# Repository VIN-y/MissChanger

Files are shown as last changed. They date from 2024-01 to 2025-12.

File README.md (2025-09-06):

# MissChanger

A Stealth Burner tool-change system for Voron 2.4 and Trident.



## Description

MissChanger aims to be a tool-changing upgrade that is compatible with both Voron Trident and Voron 2.4 (Trident compatibility is pending). While also retaining the accuracy and reliability of the MGN9H tapping system of Voron-Tap.

Other features of MissChanger includes:

* The ability to quickly and toollessly convert between tool changer mode and single nozzle mode (for when you need the full print volume of the stock printer).

* Nozzle brush dock. For cleaning the ooze and build-up after tool-change.

## Compatibility

#### Printers:

- Voron 2.4 350 (up to 5 SBs)
- Voron 2.4 300 (up to 4 SBs)

For those who want to adapt MissChanger to your own system. The Bar-Ends are 28mm each, and each dock is 80mm in width. All will be riding in the groove of the 2020 aluminium extrusion frame.

#### Toolhead:

- Stealth Burner

#### Hotend:

Any hot-ends that does not require a custom/extended main-body for the Stealth Burner should works just fine. Nevertheless, the follows are those that has been tested on the reference machine:

- Revo-Voron - Recommended.
  - It is officially supported for the Stealth Burner.
  - It has the the right amount of thermal mass to keep the nozzle temperature stable, while still have decent heat-up and cool-down time.
- Phaetus Dragon - Not recommended.
  - The heater block causing slow heat-up and cool-down. This is not ideal, since it is beneficial to lower the tool temperature when it is docked for a long period of time.
  - The cold side of the hot-end is inadequate to cool PLA in a 30°C+ chamber, eventually causing heat creep if the heater is constantly on.
  - Close proximity between the heater block to the plastic causing deformation. This does not resulted in critical failures, but the affected parts will not work on any other assembly.

#### Extruder:

All extruder that is compatible with the Stealth Burner should works just fine. Nevertheless, any added dimensions on top of the Clockwork 2 might resulted in less print area or space for other tool-heads.

**For v1:** 

* ClockWork 2 (CW2) - Default
  
  * All quoted clearance dimensions are in reference to this extruder.

* Galileo 2 Extruder (G2E)
  
  * The thumbscrew stick out ~8mm to the left. Thus, taking up more docking space than default.

## Assembly

BOM, STLs, and instructions are in the [STL_&_Assembly](./STL_&_Assembly) folder (for the latest and relevant versions), or [MissChanger Archive](https://drive.proton.me/urls/3CDH12JTMW#YhJ5K3t4AadW) (for past versions).

**<u>Note:</u>**

Through testing with material combinations such as ABS-PLA. The window for success for combination of materials that need an enclosure and those that don't are extremely tight. Achieving it require additional hardware (for active chamber temperature control), compromises (such as: weaker layer adhesion, weaker bed adhesion, etc.), and trials-&-errors for every print job. Therefore, it is advised to decide on whether the machine should or should not be enclosed before hand and stick with material combinations that has the same chamber requirements.

## Software

For the latest **Alpha** / **Beta** / **Release** version, instructions are available here: [Klipper_Config](https://github.com/VIN-y/MissChanger/tree/main/Klipper_Config).

The plugin for MissChanger is a fork of [klipper-toolchanger](https://github.com/viesturz/klipper-toolchanger), for [Tapchanger](https://github.com/viesturz/tapchanger), and it is available via GitHub at [VIN-y/klipper-toolchanger](https://github.com/VIN-y/klipper-toolchanger). MissChanger deviate greatly from the design of Tapchanger and Draftshift (Stealthchanger); thus, it's config files are not compatible upstream.

### Recommended software:

- [KIAUH](https://github.com/dw-0/kiauh) - For the purpose of managing Klipper updates, to handle any potential incompatibility issues, whenever there is a major Klipper update.
- [Klipper-Backup](https://github.com/Staubgeborener/Klipper-Backup) - Klipper-Backup is a script for manual or automated GitHub backups. It's Lightweight, pragmatic and comfortable.

## Roadmap

### v1

- [x] ~~Lock in the Tap&Change and dock design for all future versions~~ - v1.1. is the final version for the Tap&Change system for the Stealth Burner
- [x] ~~Print capability test, material combination~~ - Tested with the three most common materials
- [x] ~~Compatibility with smaller Vorons~~ - Have been shown to be compatible with the Voron 2.4 300, via a different assembly configuration (shown in the manual), which should also be compatible with the 250 Vorons.
- [x] ~~USB tool-head support~~ - Nitehawk SB USB tool-head board.
- [ ] Trident compatibility - Full compatibility will be done along side v2.

### v2

- [ ] Trident compatibility - v2 will be built directly on a Trident
- [ ] Support for additional tool-heads - A4T

## Other information

### Status definition

| Terms | Description |
| --- | --- |
| Release | Finalised.<br>All relevant components and documentations are finished and tested. |
| Beta | All relevant components are locked into a release package.<br/>However, without substantial testing or feedback. |
| Alpha | CAD designs locked in.<br>No (or incomplete) documentations. |
| Bleeding  | Everything are subjected to changes. |
| Abandoned | Old design that is no longer being persuaded. |

Note: 

* The .step and CAD project files for all but the most recent version will not be included in this repository, due to the storage/transfer limits of GitHub.

* With user feedback and further testing, the relevant version might be updated to the next tier. However, if significant changes are required, another version will be made and start at the bleeding state; and the current version will no longer be persuaded (i.e. abandoned).

## Recommendations

1. Keep tool-heads as similar as possible. 
   
   1. The more variations there are between tool-heads (i.e. control board, hot-end system, etc.), the more tuning will be need for each of them.
   
   2. Meaningful variants includes: extruder, nozzle size, nozzle material.

2. The following mods are not needed but is **recommended** to enhance the capability of MissChanger:
   
   1. [Calilantern Calibration Tool](https://vector3d.shop/products/calilantern-calibration) - MissChanger requires relatively high dimensional-accurate printed parts, to mate with each others. Therefore, it is recommended that you take the extra steps to calibrate your printer before starting the build.
   2. [Nevermore StealthMax](https://github.com/nevermore3d/StealthMax) - to regulate the chamber temperature, to allow PETG / PLA printing with the door closed; allowing them to be combined with ABS.
   3. [Spool Holder](https://www.printables.com/model/872144-spool-holder-for-2020-aluminium-extrusion) - to hold the spools on top of the machine. There are many ways to get this done, and it depends on the people's specific use-cases. The design linked here is just of my (the developer) own creation.
   4. [Inverted z-chain](https://www.printables.com/model/445298-inverted-z-chain-for-voron) - This is for the Voron 2.4 300mm, or smaller. To clear the space in front of the back gantry extrusion for the umbilicals.

3. The following mods are either **not recommended** or known to be not compatible with MissChanger:
   
   1. GE5C bearing z mount - This mod offer too much flexibility to the gantry, allowing it to sag when the z motors are disabled/un-powered. Nevertheless, it's inclusion will not cause catastrophic problems. You will just need to be careful. (I personally could not be bothered enough to remove mine) 
   
   2. Beefy front idlers - The cut off on the dock can only fit the stock front idlers.
   
   3. AWD - The cut off on the dock can only fit the stock front idlers.

## Sample







## Mods

Community members are encouraged to modify the the CAD where they see fit. They can contribute back to the project by either:

1. Creating a Pull Request, and add the modded files into the [UserMods](./UserMods) folder.

2. Reach out and send me the STEP files.

Modded items are not tested or officially supported. However, if it contains good ideas, it will be implemented into the official design down the line. The originator of the ideas will be included in the list bellow as a contributor.

... So, don't give yourself a weird name, please.

## Support

If you have any question, please FIRST check the [MissChanger Wiki](https://github.com/VIN-y/MissChanger/wiki)

If you still have any question, you can reach me at:

* `@vin` in the [Voron Toolchangers](https://discord.gg/qrb6HXNYxs) discord
* `@vinny_69 V2.6365` in the [VORONDesign](https://discord.gg/voron) discord
* [@vin-y.bsky.social](https://bsky.app/profile/vin-y.bsky.social) on Bluesky

## Contributors

* `@psychosis5150` in the [Voron Toolchangers](https://discord.gg/qrb6HXNYxs) discord
* `@pendorbound` in the [Voron Toolchangers](https://discord.gg/qrb6HXNYxs) discord

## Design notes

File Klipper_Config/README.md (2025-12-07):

# Table of Contents

1. [Introduction](#1-introduction) 

2. [Versions](#2-versions) 

3. [Software](#2-software) 
   
   3.1. [Installation](#31-installation) 
   
   3.2. [Configuration](#32-configuration) 

4. [Calibration](#4-calibration) 
   
   4.0. [Tap&Change burn-in](#40-tapchange-burn-in) 
   
   4.1. [Park position calibration](#41-park-position-calibration) 
   
   4.2. [Input Shaper (optional)](#42-input-shaper-optional) 
   
   4.3. [Calibrate offsets](#43-calibrate-offsets) 

5. [Test and Troubleshoot](#5-test-and-troubleshoot) 
   
   5.1. [Offsets](#51-offsets) 

6. [Tool-change Tuning](#6-tool-change-tuning) 

7. [Slicer Profile](#7-slicer-profile) 

---

# 1. Introduction

Although setting up the config for MissChanger will change some aspects of your printer, it is still recommended that you start the project with a functional printer with Voron-Tap, then add MissChanger and one tool-head at a time.

This document will not guide you through the set up of CAN bus or the physical mounting of the related hardware (i.e. U2C and tool-head board), please refer to the manufacture’s manual for that.

---

# 2. Versions

There are 3 versions for the software, the sample user configs for which are placed in the relevant folder: [1_Main](./1_Main) / [2_Beta](./2_Beta) / [3_Alpha](./3_Alpha).

**Note:** User configs are files that will needed to be set-up on the user's side.

---

# 3. Software

This section aims to provide a guide through the installation process of the software and setup the config.

## 3.1. Installation

To install the [klipper-toolchanger](https://github.com/VIN-y/klipper-toolchanger) plugin, run the following installation script using the following command over SSH. This script will download this GitHub repository to your RaspberryPi home directory, and symlink the files in the Klipper extra folder.

Before installation. For those who are switching branches. You will need to run the uninstall script in below, in **section 3.1.2**.

---

### 3.1.1. Install

1. For normal use:

```
wget -O - https://raw.githubusercontent.com/VIN-y/klipper-toolchanger/main/scripts/install.sh | bash
```

2. For Beta test:

```
wget -O - https://raw.githubusercontent.com/VIN-y/klipper-toolchanger/beta/scripts/install.sh | bash
```

3. For Alpha test:

```
wget -O - https://raw.githubusercontent.com/VIN-y/klipper-toolchanger/alpha/scripts/install.sh | bash
```

*Note 1: You will need to reboot the printer whenever there is an update for the add-on.*

---

### 3.1.2. Uninstall

Some manual changes will still need to be done in the user space (i.e. the section that is accessible via the web interface). These settings / files / folders tend to contain information and calibration values specific to your printer. Thus, it is advised that you create a backup before deletion. This includes:

* The `config` folder

* The `misschanger_settings.cfg` file

* Relevant tool-head config file

* Relevant settings in `printer.cfg`

* `moonraker.conf` registry

To fully uninstall the back-end, run one of the following commands over SSH. Make sure to select the link that is relevant to the version that is currently installed on the printer.

1. For normal use:

```
wget -O - https://raw.githubusercontent.com/VIN-y/klipper-toolchanger/main/scripts/uninstall.sh | bash
```

2. For Beta test:

```
wget -O - https://raw.githubusercontent.com/VIN-y/klipper-toolchanger/beta/scripts/uninstall.sh | bash
```

3. For Alpha test:

```
wget -O - https://raw.githubusercontent.com/VIN-y/klipper-toolchanger/alpha/scripts/uninstall.sh | bash
```

---

## 3.2. Configuration

The **sample configuration files** can be found in the relevant folder above.

The following, starting from **Step 1**, are the recommended steps to get the software up-and-running using the default set of macros. Following the guide will make it easier for you to get support.

The default macros will be managed and updated together with the software stack.

---

### Step -1: Customisation

If you are comfortable with it, you are welcome to by-pass the default macros and play with the configs files to your liking. If you find any errors or room for improvement, feel free to reach out to me to get it fixed, via a GitHub pull request or otherwise.

For building your custom macro:

1. Check where the relevant macro is saved, using the [code stack breakdown](./code_stack_breakdown.pdf) 

2. Download the relevant macro config file, in the [klipper-toolchanger](https://github.com/VIN-y/klipper-toolchanger/tree/main/macros) repository (or straight from your web interface)

3. Import the config file back using the web interface

4. `include` it back into`printer.cfg`

5. Comment-out (or delete) the reference to the file that the new config replaces, in `printer.cfg`

6. Save and Restart

7. Start editing the file to your liking

---

### Step 0: Pre-configuration

These are settings that are in the default Klipper that should to be enabled:

1. [exclude_object] - [Exclude Object](https://youtu.be/QTwRZ_M159Q?si=oV987KDLM-wXsYoE), video guide by [ModBot](https://www.youtube.com/@ModBotArmy) 
2. [skew_correction] - calibrate with [Vector3D CaliLantern](https://vector3d.shop/products/calilantern-calibration) 
3. [input_shaper] - see section **4.2.** 
4. [bed_mesh] - This should have already been configured. However, make sure that there is a bed mesh profile named "default", for the PRINT_START to fallback to if needed.

---

### Step 1: Back-up your running system

Through your web interface:

1. Select all of your config files

2. Download it to your computer

---

### Step 2: Set up printer.cfg

You can check the sample `printer.cfg` in the relevant folder above as reference.
`macro-general.cfg` and `macro-testing.cfg` are optional macros for operations (do not include them in printer.cfg if not used).

Each variable has been given a short description on what they do. Some variables can be used to disable functionalities, such that you will not need to comb through the configs to find and edit them out. The key sections are:

1. Add the **Section Variables** section.
   
   These sections need to be placed just before the **SAVE_CONFIG** section, as shown in the sample `printer.cfg`. Everything below the `Section Variable marker` will be swapped in and out upon the `CONFIG_TOGGLE` macro. If a function setting already exists somewhere else in printer.cfg, the old function will need to be transferred to the new location and updated.
   
   The critical settings that need to be changed are as follows:
   
   - `[gcode_macro _home]` needs to adjusted with the appropriate `xh` and `yh` which represents the centre of the new build area (i.e. 150 (x), 210 (y) for a 300x300 bed).
     
     - `variable_dock` is the indicator of which config is being used.
       
       1. Before installing the dock and other tool-heads, set `variable_dock` to `False`. 
       
       2. Set up T0 (the reference tool-head), see **Step 3**. The `[quad_gantry_level]` (or `z_tilt`, for Trident), and `[bed_mesh]` stay the same the same as stock.
       
       3. After T0 is operational, run `SAVE_CONFIG_MODE`
       
       4. From the web interface, see if the everything below the `Section Variables` has been saved to a .cfg file in the "config" folder.
       
       5. Change `variable_dock` to `True`
       
       6. Install the physical dock. The `[quad_gantry_level]` or `z_tilt` (for Trident), and `[bed_mesh]` **MUST** be updated, as shown in the next 2 bullet points.
   
   - `[quad_gantry_level]`, or `z_tilt` (for Trident), increase the y position of the front 2 `points:` to `130`, to avoid crashing into the dock.
   
   - `[bed_mesh]`, make sure that `mesh_min: 30,130` , to avoid crashing into the dock.

2. If it exists in **printer.cfg**, disable `[safe_z_home]` (comment-out or delete)

3. Add relevant variable (see the code snippet below) under **SAVE_CONFIG**. `[tool_probe T0]` and  `[extruder]` are needed no matter what your setup as it is the reference / default tool-head.
   
   ```
   #*# <---------------------- SAVE_CONFIG ---------------------->
   #*# DO NOT EDIT THIS BLOCK OR BELOW. The contents are auto-generated.
   #*#
   #*# [tool_probe T0]
   #*# z_offset = -0.817500
   #*#
   #*# [extruder]
   #*# control = pid
   #*# pid_kp = 39.282
   #*# pid_ki = 4.365
   #*# pid_kd = 88.386
   #*#
   ```

4. For each additional tool-head, you will need an associated set of  `[tool t(x)]`, `[tool_probe T(x)]`, and `[extruder(x)]` sections. **It is RECOMMENDED** to add and test the tool-heads, one at a time. For example:
   
   ```
   #*# [tool T1]
   #*# gcode_x_offset = -0.225000
   #*# gcode_y_offset = 0.590625
   #*# gcode_z_offset = 0.470000
   #*#
   #*# [tool_probe T1]
   #*# z_offset = -0.622500
   #*#
   #*# [extruder1]
   #*# control = pid
   #*# pid_kp = 33.912
   #*# pid_ki = 3.325
   #*# pid_kd = 86.477
   ```

*NOTE 1: Your printer will be throwing errors at this point, until the software is fully setup.* 

*NOTE 2: The variables will need to be calibrated to match your hardware.*

---

### Step 3: Make the reference tool-head config file

Use the `T0-SB2209-Revo-LDO.cfg` in [Sample_Config](./Sample_Config) folder as reference.

1. Transfer the items relating to the tool-head from your `printer.cfg` to a separate file:
   
   * `[mcu EBBCan0]` - the MCU for your tool-head, named to your liking, i.e. EBBCan0.
   
   * `[adxl345]` - The accelerometer on the tool-head.
   
   * `[resonance_tester]` 
   
   * `[temperature_sensor]`
   
   * `[extruder]`
   
   * `[tmc2209]` - that is associated extruder motor
   
   * `[verify_heater]`
   
   * `[heater_fan]`
   
   * `[neopixel]` - if applicable
   
   * `[tool_probe]` 
     
     <mark>NOTE:</mark> the `activate_gcode:` for the item has been replace with the macro `_TAP_PROBE_ACTIVATE`, with the flag `HEATER=extruder`. This flag <mark>NEEDS TO BE SET TO THE RIGHT "EXTRUDER"</mark>. Failure to do so may result in damage bed surface.

2. Replace `[fan]` with `[fan_generic T0_partfan]`

3. Add the following item and macro:
   
   * `[gcode_macro T0]` - for tool switching
   
   * `[tool T0]` - associate the items above to T0 and provide tool specific variables (which will need to be adjusted later).

---

### Step 4:

Include tool-head config in the session variables are in `printer.cfg`, as shown in the relevant sample config.

*Note: At this point, the printer should be able to have a firmware restart without (or with minor) errors.* 

---

### Step 5: Calibrate and test T0

1. For safety reasons, remove the dock and any attached tool-head other than T0.

2. Run `FIRMWARE_RESTART` and fix any problem that arise ;)

3. Run `G28` and `QUAD_GANTRY_LEVEL` 

4. Check that:
   
   * The printer homes Y before X
   
   * Quad gantry level front points are at Y = 130
   
   * Extruder PID is correctly set and applied (no error / no bouncing temperature)

5. Re-mount the dock

6. Calibrate extruder `rotation_distance`

7. Calibrate heater PID

8. Calibrate the park position, see **section 4.1.** 

9. Calibrate the `z_offset`, see **section 4.3.** 

10. (optional) Calibrate input shaper, see **section 4.2.** 

11. Save & Restart

---

### Step 6: Make the next tool-head and its config file

1. Follow the hardware assembly guide from the manufacture of the relevant hardware, i.e extruder, tool-head board, etc.

2. Mount the dock and temporarily mount the new tool-head to the dock.
   
   <mark>CAUTION:</mark> **DO NOT** try to make the printer pick up the new tool yet.

3. Use `T1-SB2209-Revo-LDO.cfg` (and others) config file as references. Make, calibrate, and test the config files for the other tool-heads.

4. Include tool-head config in the session variables in `printer.cfg`, as shown in the code block in **step 2.3**.

5. Copy and paste the associated set of `[tool t(x)]`, `[tool_probe T(x)]`, and `[extruder(x)]` to the **SAVE_CONFIG** section, if they are not already there.

6. Save & Restart

---

### Step 7: Calibrate and test tool-head

If this is the first tool-head you made beside the reference tool-head, then you will need to test the max y position of your set up:

1. Run `G28`

2. Manually nudge the tool-head to right behind (but not touching) a docked tool (via the web interface), 

3. Note down the Y position of that location

4. If the y location is greater than 120 mm, then you will need to update the `params_safe_y` value in `[toolchanger]` in `misschanger_settings.cfg`

5. Save & Restart

Otherwise:

1. Calibrate extruder `rotation_distance`

2- Calibrate heater PID

3. Save & Restart

4. Run `G28` and `QUAD_GANTRY_LEVEL`

5. Calibrate the park position, see **section 4.1.** 

6. Calibrate the `z_offset`, see **section 4.3.** 

7. (optional) Calibrate input shaper, see **section 4.2.** 

---

### Step 8: Other macros

* `macro-general.cfg`

* `macro-test.cfg`

These configs tend to be points of customisation for many. Therefore, the included files are intended to be inspirations for your own macros. They contain commands and functionalities that may not be needed or are not relevant to your printer.

---

### Step 9: Single tool-head config

1. Run `SAVE_CONFIG_MODE` to save the current setup.

2. Check if the save was made correctly, in the **config** folder.

3. In the Section Variable section in **printer.cfg**:
   
   1. Comment out all included tool-head configs other than T0
   
   2. Under `[gcode_macro _home]`:
      
      1. Set an appropriate `xh` and `yh` which represent the centre of the new build area (i.e. 150 (x), 210 (y) for a 300x300 build plate).
      
      2. Set `variable_dock` to `False`
   
   3. Revert `[bed_mesh]` and `[quad_gantry_level]` to the original values of the stock machine (without the tool-changer bits)
   
   4. Delete all `#*# [tool T(x)]`, `#*# [tool_probe T(x)]`, and `#*# [extruder(x)]` objects, under the `SAVE_CONFIG` section.
      
      * **EXCEPT:** the `#*# [tool_probe T0]` and `#*# [extruder]` object.  

4. Save, but no restart is needed.

5. Run `SAVE_CONFIG_MODE` and check if the file is correctly saved.

Now, the `CONFIG_TOGGLE` macro will allow you to toggle between these 2 configs.

---

# 4. Calibration

This section assumes that the new tool-head has been assembled, wired up, and has been recognised by Klipper.

## 4.0. Tap&Change burn-in

The following steps are for the burn-in of the Tap&Change mechanism. This is so that it can sort out any misalignment due to print tolerance and assembly. Through testing, it has been shown that this only need to be done once for every Tap&Change rail-side (there is only one in the system).

1. Setup to the variable for `SHAPER_CALIBRATE`, to your liking

2. Manually mount T0

3. Run `G28`

4. Bring the tool-head to 10 mm above the centre of the bed

5. Turn on the bed heater

6. Turn on the chamber fan (if exist)

7. Wait until the tool-head (i.e. "Extruder") temperature reached ~40°C (or ~10 mins if you don't have a chamber temperature sensor)

8. Run `SHAPER_CALIBRATE` - Note: This is only meant to shake the tool-head around in its mount. Do not save the input shaper result.

9. Repeat step 4 - 8 until the tool-head can fall into the mount on it's own weight when manually removed and replaced.

---

## 4.1. Park position calibration

1. Run `G28` and `QUAD_GANTRY_LEVEL`  - if not already done

2. Run `G1 Z150 F9000` 

3. Run `STOP_TOOL_PROBE_CRASH_DETECTION` 

4. Loosen the bolts on the bottom of the dock of the relevant dock (so it will spin around the bar)

5. On the web interface, in `Setting > Control` add `0.1` and remove `100` in the `Move distance increments X & Y axes (in mm)` 
   
   *Note: This is temporary for this step only, and can be reverted later.*

6. Set the dock toolhead cradle at the 'empty' position in the dock assembly, i.e. at the bottom of the ramp.
   

7. Use the web interface, nudge the tool-head into the correct x-position. This can be tested by nudging the y-position in and out to see which side of the tool-head touches the dock first. Then adjust the x-position such that both sides of the dock touch the tool-head at the same time.
   

8. Copy and paste the current x-coordinate into the `params_park_x:` of the config file of the current tool-head

9. Save it, **BUT DON'T RESTART**

10. Nudge the y-position until the toolhead is fully seated in the dock toolhead cradle.
    
    1. Make sure that the whole dock-bar isn't being lifted up in the extrusion grooves.
    
    2. Make sure the toolhead is fully seated in the dock toolhead cradle before it starts being lifted up the ramp. Check it by nudging it back and forth 10mm.
    
    3. If step 10.1 and 10.2 are not met, adjust the Bar End spacers to fit. TIP: the distance for the spacers should be the same for both sides.

11. Tighten the bolts on the bottom of the dock (locking it in place)

12. Nudge the y-position until the dock is at the peak of the ramp. The dock is tough enough to handle a bit of pressure from the gantry so you can keep nudging the y-position until the dock flexes a bit, then back it off.

13. Run:
    
    ```
    G91
    G1 Y+80 F6000
    G90
    ```

14. Copy and paste the current y-coordinate into the `params_park_y:` of the config file of the current tool-head

15. Save it

16. Run `FIRMWARE_RESTART`

17. Run the `TEST_DOCKING` macro

---

## 4.2. Input Shaper (optional)

*Note: To avoid Klipper from throwing errors, the parameters for input shaper are pre-populated in* `toolchanger.cfg` *and in each tool-head config file. Nevertheless, it is best to calibrate it for each available tool-head.*

1. Enable (un-comment) the `[adxl345]` and `[resonance_tester]` in the config of the tool-head that is to be calibrated

2. Disable (comment out) the `[adxl345]` and `[resonance_tester]` in the config of the other tool-heads

3. Save & Restart

4. Mount the tool-head that is to be calibrated

5. Run `G28` and `QUAD_GANTRY_LEVEL`

6. Run `SHAPER_CALIBRATE` - **BUT, DO NOT SAVE**

7. From the console output, save the following parameters into the tool-head config (at the bottom of the `[tool Tx]` section)
   
   ```
   params_input_shaper_type_x: ...
   params_input_shaper_freq_x: ...
   params_input_shaper_damping_ratio_x: ...
   params_input_shaper_type_y: ...
   params_input_shaper_freq_y: ...
   params_input_shaper_damping_ratio_y: ...
   ```

8. Save & Restart

---

## 4.3. Calibrate offsets

### 4.3.1. Calibrate reference z-offset

1. Mount tool-head T0

2. Go to T0 config file. Make sure:
   
   - `z_offset` under `[tool_probe T0]` is commented out
   
   - Every other offsets to `0`; i.e. `x_offset` and `y_offset`
   
   - Save it, **BUT DON'T RESTART**
   
   

3. Run `G28` and `QUAD_GANTRY_LEVEL` 

4. Run `PROBE_CALIBRATE` on the console and go through the process with the normal paper test.

5. <u></u>Run `SAVE_CONFIG` - which will restart your printer

6. Go to `printer.cfg`

7. Copy the z-offset value from:
   
   ```
   #*# [tool_probe_endstop]
   #*# z_offset = {value}
   ```
   
   And, paste it to:
   
   ```
   #*# [tool_probe T0]
   #*# z_offset = {value}
   ```

8. Delete:
   
   ```
   #*# [tool_probe_endstop]
   #*# z_offset = {value}
   ```
   
   *Note: It will not be used regardless of whether it is there or not.*

9. Save & Restart

*Note: It is key that you get the z_offset correct for the T0, as it will be used to extrapolate other offsets later on. Therefore, it is worth diverging from these instruction if you have a preferred way to set your the z-offset.*

---

### 4.3.2. Calibration probe setup

At this stage, you should have:

- The calibration probe assembled, tested, and installed

- T0 z-offset calibrated

This section will guide you through the calibration of the machine specific variable `trigger_to_bottom_z`, which will allow you to automate the z-offset of the tool-heads that are not T0. *Note: This should be your go to variable to adjust whenever you ran into z-offset issue.*



### Setup:

1. Open `misschanger_settings.cfg`

2. Setup `[tools_calibrate]` with the correct `pin`, for the LubeBalls (or Nudge)

3. Save and restart

4. Test calibration probe, by touching the it with your finger and run `TOOL_CALIBRATE_QUERY_PROBE`
   
   

5. Open `printer.cfg`

6. Set the approximate X and Y location of the Nudge pin in `[gcode_macro _static_variable]`. Note: you can find out the XY position by homing and moving the tool-head in place with the web UI or Klipper Screen.
   
   

7. Save and restart

### Steps:

1. Go to `printer.cfg` and record the `z-offset` for `[tool_probe T0]`, which should be at (or near) the bottom of the file

2. Mount tool-head **T0** and make sure it's nozzle is clean

3. <mark>**!!! MAKE SURE THE CALIBRATION PROBE IS NOT MOUNTED !!!**</mark>

4. Run `G28` and `QUAD_GANTRY_LEVEL`

5. Mount the calibration probe to the bed.

6. Run `CALIBRATE_TRIGGER_BOTTOM`. If it is a fresh calibration probe, it is worth redoing this step until the suggested value is consistent at +/- 0.005mm. 

7. Copy the proposed offset on the console to the `trigger_to_bottom_z:` in `[tools_calibrate]`.

8. Save and restart

9. Run `CALIBRATE_OFFSETS TOOL=0` - But, **DON'T RESTART**

10. Check if proposed z-offset to be +-0.01mm of the recorded `z_offset` in **step 1**.

11. Run `CALIBRATE_OFFSETS TOOL=0` 2-3 more times to make sure the measured value is consistent.

**Your calibration probe is ready.**

*Note: It is worth mentioning that there are other ways to calibrate your offsets, such as the visual based solution from [Ember](https://www.emberprototypes.com/products/cxc) or the calibration print that you can get from [Printables](https://www.printables.com/model/201707-x-y-and-z-calibration-tool-for-idex-dual-extruder-). Each have their pros and cons in terms of accuracy and cost. However,  a physical contact probe is currently the only way to automatically calibrate all relevant offsets.*

---

### 4.3.3. Other tool-head(s)

### Steps:

1. <mark>**!!! MAKE SURE THE CALIBRATION PROBE IS NOT MOUNTED !!!**</mark>

2. Make sure all tool-heads are cold (near room temperature)

3. Make sure all nozzles are clean

4. Make sure all tool-head config file (except T0) has the following variables disabled (commented out):
   
   - `gcode_x_offset` 
   
   - `gcode_y_offset` 
   
   - `gcode_z_offset` 
   
   - `z_offset` 
   
   

5. Save it, **BUT DON'T RESTART**

6. Mount tool-head T0

7. Run `G28` and `QUAD_GANTRY_LEVEL`

8. Mount the calibration probe

9. Run `CALIBRATE_OFFSETS` - the process is automatic, but you can specify a specific tool-head

10. Run `SAVE_CONFIG`

If you has the calibration probe. There is a likelihood that the `CALIBRATE_OFFSETS` procedure cannot be completed. If so:

1. set `variable_calibration_abs_z_seperately` to `1` in `[gcode_macro _static_variable]` in **printer.cfg**.

2. Mount tool-head T0

3. Run `G28` and `QUAD_GANTRY_LEVEL` 

4. Run `CALIBRATE_ABSOLUTE_Z` 

5. Run `SAVE_CONFIG`

---

### 4.3.4. Clean dock

#### Steps:

1. Install the clean dock in your preferred slot on the gantry

2. Approximate the x position of the centre of the dock (where the brush is)

3. Add the aforementioned x position into `printer.cfg`. In `variable_clean_dock_x` under `[gcode_macro _static_variable]`.

#### Optional steps, for auto mid-print clean:

1. Set-up the `variable_clean_threshold` under `[gcode_macro _static_variable]`. "150" means that the print needs to take up ~50% of the bed before triggering a mid-clean print.

2. List the materials that need to have their associated tool-head cleaned in `misschanger_settings.cfg`. For example:
   
   ```
   params_need_clean_materials: ['PETG', 'FLEX']
   ```

---

# 5. Test and Troubleshoot

## 5.1. Offsets

It is important to test if the `z_offset` and `gcode_z_offset` are set-up and applied correctly. A misconfigured `z_offset`/`gcode_z_offset` can cause the nozzle to be dragged on the bed, risking damage. Please follow the steps below to test the config, before you start printing.

### Part 1: Check the z_offset of T0

1. Make sure the printer is cold (near ambient temperature).

2. Run `G28` and `QUAD_GANTRY_LEVEL` with T0

3. Run `G1 X175 Y235 Z10 F9000` (centre of print area)

4. Run `G1 Z0 F9000` 

5. Test the z-offset with the paper test. - If it is good then you set up the `trigger_to_bottom_z` value correctly.

6. If it does not work:
   
   1. baby step the z position to the correct position
   
   2. adjust `trigger_to_bottom_z` accordingly using the baby stepped amount.
   
   3. then, rerun `CALIBRATE_OFFSETS TOOL=0`.
   
   4. retry step 1 to 3 until the paper test succeeds.

### Part 2: Check the gcode_z_offset of the other tools

1. Go through step 1 and 2 of **Part 1**, above.

2. Switch to next tool, via the web UI or Klipper Screen.

3. Go through step 3 to 6 of **Part 1**, above.

4. If it does not work. rerun `CALIBRATE_OFFSETS TOOL=[x]` for that tool-head (or all of them).

### Part 3: gcode_x_offset and gcode_y_offset

To validate `gcode_x_offset` and `gcode_y_offset`, you just need to print something and see if they are set-up and applied correctly. Alternatively, you can also buy and use [Ember Camera Assisted XY](https://www.emberprototypes.com/products/cxc) to validate them.

---

# 6. Tool-change Tuning

The speed and path of the default tool-change routine in `misschanger_settings.cfg` is tuned for reliability. It is slower and has more steps than needed.

For a smooth running MissChanger. The `params_path_speed` can be increased and some of the "Wiggle wiggle", in the path, can be disable.

---

# 7. Slicer Profile

## 7.1. Custom Start G-code

Copy and paste the following code into your slicer.

*Note: It needs to stay as a single line of gcode.*

```
PRINT_START BED_TEMP=[first_layer_bed_temperature] FIRST_LAYER_PRINT_SIZE=[first_layer_print_size] TOOL=[initial_tool] TOOL_TEMP={first_layer_temperature[initial_tool]} {if is_extruder_used[0]}T0_TEMP={first_layer_temperature[0]} T0_Fil={filament_type[0]}{endif} {if is_extruder_used[1]}T1_TEMP={first_layer_temperature[1]} T1_Fil={filament_type[1]}{endif} {if is_extruder_used[2]}T2_TEMP={first_layer_temperature[2]} T2_Fil={filament_type[2]}{endif} {if is_extruder_used[3]}T3_TEMP={first_layer_temperature[3]} T3_Fil={filament_type[3]}{endif} {if is_extruder_used[4]}T4_TEMP={first_layer_temperature[4]} T3_Fil={filament_type[4]}{endif} {if is_extruder_used[5]}T5_TEMP={first_layer_temperature[5]} T5_Fil={filament_type[5]}{endif}
```



Also. Disable the following option:



## 7.2. Slicer Bed Shape

The printer bed shape need to be set as shown below to avoid collisions with the dock during printing.

Depending on the umbilical mounting solution on the tool-head side, the lost y can be between 120mm to 140mm.

*Note: It can be seen here that the max print height was set to 235mm. This is recommended for new machines to avoid umbilical tangling. However, if you are willing to do some tuning to the tension of the umbilical or add a top hat to the system, the max print height can be increased to 250mm or 300mm.*

### For printers with 350mm beds:



### For printers with 300mm beds:



## 7.3. Multiple Extruders

Enable **Ooze Prevention**.

This setting will allow you to reduce the docked nozzle temperature, to prevent over cooking the filament. Furthermore, it will effectively act as reheat command for when the system is recovering from a failed tool-change.

Even if you don't want it to drop the temperature, still enable it, then set the `Temperature variation` to -25°C. This setting will emit a nozzle heating command after tool-change.



## 7.4. Speed profile

Although, you might want to tune your own speed profile for the best performance. Here is a slow and reliable profile to get you started with.



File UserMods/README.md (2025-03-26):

## For all mods to the CAD

Please put your custom files here, in a folder of your Github profile name (or Discord name), i.e.:

`[your-profile-name]`/`[custom-files/folder]`

Please also includes a `README.md` file, with the descriptions / instruction of for the mod. Additional photos will also be appreciated.

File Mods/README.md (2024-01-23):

## For all mods to the software / CAD
Please put your custom files here, in a folder of your Github profile name. i.e.:

`[your-profile-name]/[custom-files/folder]`

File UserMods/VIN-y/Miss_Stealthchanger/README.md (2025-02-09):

# Miss Stealthchanger

This is a mod to the Stealthchanger v1.1 to make it compatible with MissChanger's docking system. See it working via this [YouTube video](https://youtube.com/shorts/WBkSGx4JyOY?si=XXWXMF8TNKqw9jsA).

## Software:

* No software change needed

## Hardware:

* This mechanism replaces the Tap&Change system. It includes:
  
  * SC_TH-side_mod.stl
  
  * Shuttle_Keeper_6mm_MGN12H.stl
  
  * Shuttle MGN12 (Without belt grooves).stl
  
  * X-trigger_v1-Body001.stl

* Stealthchanger Assembly Guide is attached

* This mod ONLY support the Stealth Burner version of Stealthchanger

* For other mounting options of the Shuttle, visit [DraftShift/StealthChanger](https://github.com/DraftShift/StealthChanger)

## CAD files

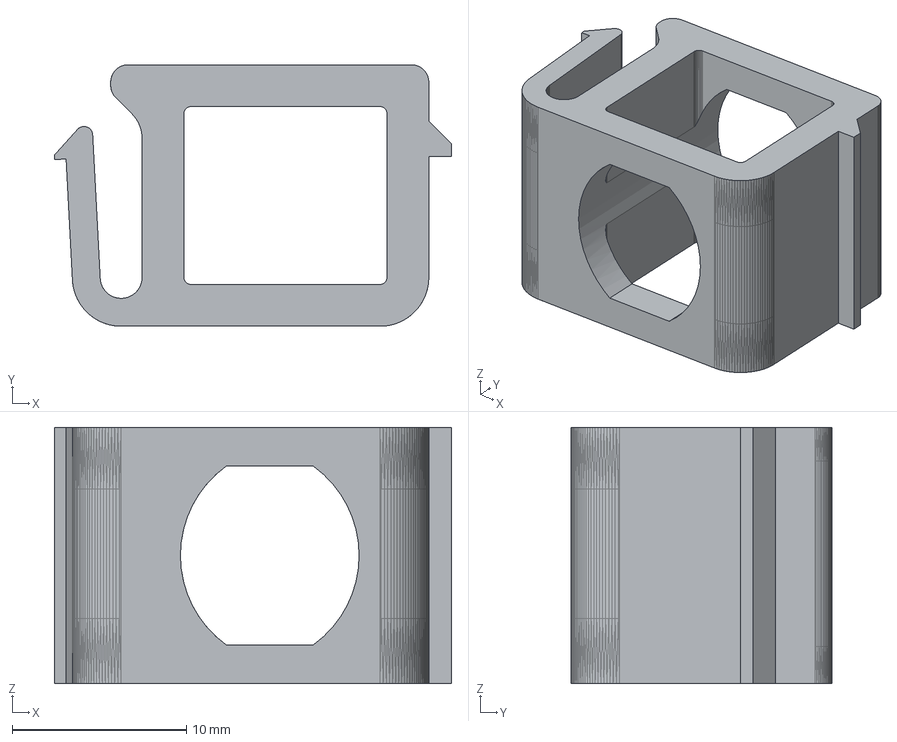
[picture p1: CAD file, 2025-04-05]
CADs/v1_MVP/Optional/DC_Barrel_Panel_Mount/11_DC_Barrel_Keystone-Keystone.step
22.8 x 15.0 x 14.7 mm

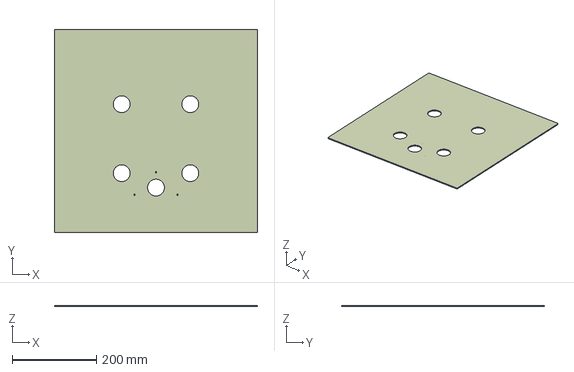
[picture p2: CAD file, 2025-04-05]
CADs/v1_MVP/Optional/Nevermore_Stealthmax/10_NM_StealthMax_Mod-Top_Panel_350_Drill.step
483.0 x 483.0 x 3.00 mm

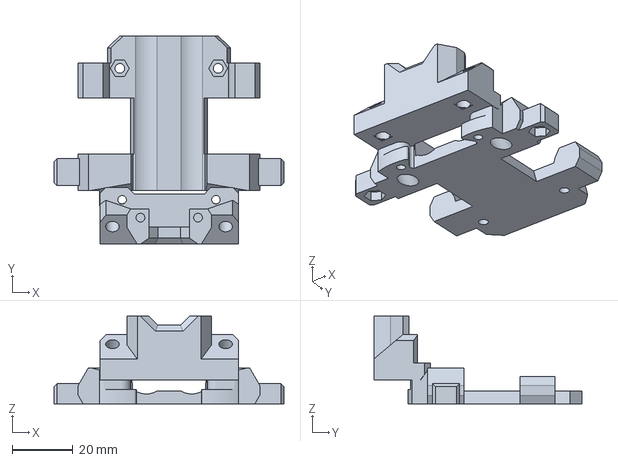
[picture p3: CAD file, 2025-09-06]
STL_&_Assembly/1_Tap&Change/Tap&Change-Front_TH_Side_Mono.3mf
76.0 x 68.9 x 29.0 mm

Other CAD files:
STL_&_Assembly/6_Optionals/Nevermore_StealthMax/M_2.0_MainChamber.stl
STL_&_Assembly/1_Tap&Change/Endstops_Assembly-v0.6.stl
CADs/v1_MVP/Endstops_Assembly-v0.6.step
STL_&_Assembly/1_Tap&Change/MGN9_Assembly_Tool.stl
CADs/v1_MVP/Tap&Change-v3.1_TH_Side.step
STL_&_Assembly/2_XLR_Panels/z_chain_bottom_anchor_mirror.stl
STL_&_Assembly/3_Dock/Bar_Ends Holder_A v1_9.stl
STL_&_Assembly/4_Calibration_Probe/Calibration_Probe_Dock_x2.stl
STL_&_Assembly/4_Calibration_Probe/Lubeballs/Luballs_Probe-Top.stl
STL_&_Assembly/4_Calibration_Probe/Nudge/wobbler_5mm.stl
STL_&_Assembly/5_Others/CW2-umbilical_anchor/CAN_Cable-Holder.stl
STL_&_Assembly/5_Others/G2E-umbilical_anchor/G2E_standoff_2_mod.stl
STL_&_Assembly/5_Others/PTFE_Panel.stl
STL_&_Assembly/6_Optionals/DC_Barrel_Panel_Mount/11_DC_Barrel_Keystone-Keystone.stl
UserMods/Psychosis5150/Idle Dock Mount/Dock Mount.stl
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

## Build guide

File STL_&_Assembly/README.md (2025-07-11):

# Introduction

This folder contains the STLs, config files, and instructions for both the latest and past version of MissChanger.

Each versions are enclosed in their own folder in the [MissChanger Archive](https://drive.proton.me/urls/3CDH12JTMW#YhJ5K3t4AadW). These folder should contains all the information that is available and relevant to that version of the system. Nevertheless, this directory structure was not fully fleshed out until v1.1, and CAD models reservation were not properly done until v1.2. Therefore, the documentation for versions that are older than v1.1 might not be functional, and no CAD file older than v1.2. is available.

## Situational / Optional / Mods

These following attachments are extras that will expand the capability of tool-changer system. Nevertheless, they were developed by others and does not share the same design language as MissChanger (i.e. difference print parameters).

| Mod | Description |
| --- | --- |
| [Nevermore Stealth Max](./6_Optionals/Nevermore_StealthMax)<br> + [DC Barrel Panel Mount](./6_Optionals/DC_Barrel_Panel_Mount) | - With modded flow chamber<br>- Cable management for Nevermore Stealth Max |
| [Galileo 2 + LDO Nitehawk SB USB cable strain relief](./5_Others/G2E-umbilical_anchor) | For Galileo 2 + LDO Nitehawk SB USB |
| [Inverted z-chain](https://www.printables.com/model/445298-inverted-z-chain-for-voron) | Recommended for the Voron 2.4 300mm, or smaller. To clear the space in front of the back gantry extrusion for the umbilicals. |

# Summary

| Version | Status | Remarks |
|:---:|:---:| --- |
| v0.0 | Abandoned | The design has been proven to lack durability in the testing phase. |
| v1.0 | Beta | Although functional, several reliability and usability problems were found. |
| v1.1 | Alpha | Fixes problems found in v1.0.<br/>Tool-changer reliability tested and proven. It will be carried forward, unless stated otherwise.<br/>The Nevermore StealthMax is added as optional chamber temperature management. |
| v1.2 | Beta | Add support for Voron 2.4 300mm.<br/>Add support for USB tool-heads.<br/>Add G2E official support.<br/>Revamp software stack and bug fixes.<br/>Preliminary Trident support. |
| v1.2.1  | Beta | Klipper compatibility fix.<br/>Move fan control to the the back-end, for smoother operation.<br/>Add more user controllable variables.<br/>Separate the `Klipper_Config`, to allows for software hot fix without the need to create another release. |
| v1.2.2  | Release | Minor updates to CAD.<br/>Update documentations. |

# Change Log

### v1.2.2 - minor update for Release 1

- Update Endstops Assembly for easier post-processing.

- Update documentation.

### v1.2.1 - Hot fix and add features

* Klipper compatibility fix.

* Move fan control to the the back-end, for smoother operation.

* Add more user controllable variables.

* Separate the `Klipper_Config`, to allows for software hot fix without the need to create another release.

### v1.2 - Polish hardware and revamp software

- Remigrating the project back to FreeCAD, because Ondsel ran out of funding and shutdown.

- Added official Nitehawk SB USB tool-head board.

- Voron 2.4 300 compatibility established, tested by `@psychosis5150`.

- Update the design of the Nudge Mount, for broader compatibility and increase durability.

- Update XLR panel design for better compatibility and alignment.

- Add official support for the G2E.

- Introducing the Lubedballs probe, as an alternative to the Nudge probe. Intended as an easier system to build.

- Fix some compatibility issue for Voron Trident.

- Bug fixes and revamp software stack:
  
  - Added changes from [DraftShift/klipper-toolchanger](https://github.com/DraftShift/klipper-toolchanger). This fork faster moving and has more features on top of [viesturz/klipper-toolchanger](https://github.com/viesturz/klipper-toolchanger). Nevertheless, it is noted that Viesturz is still slowly adding features to his extension. Therefore, future updates to [VIN-y/klipper-toolchanger](https://github.com/VIN-y/klipper-toolchanger) (for MissChanger) may adopt features from either of the for mention repository, where they may fit for the project.
  
  - Deprecate `multi-fan` to re-enable the ability to control the part cooling fan with the GUIs.
  
  - Establish the structure of the software stack, to have a low barrier of entry while still allow customisation.
  
  - Revamp the tool-change routine, to avoid firmware crashing or unsafe movement during pick-up.
  
  - Add fail to drop-off detection.
  
  - Fixed the bug where the `gcode_z_offset` not correctly clear out after tool-change.
  
  - Revamped `CALIBRATE_OFFSETS` routine:
    
    - To check for proper probe placement before starting the session.
    
    - Add an option to run the routine with or without absolute z calibration. For over sensitive probes.
  
  - Add a macro to calibrate trigger bottom. So the printer don't need to be restarted and homed multiple times during calibration.
  
  - Fix the bug where the QGL failure is not detected in `PRINT_START`.
  
  - Fix compatibility issue with PrusaSlicer 2.9.0+, where the XY coordinate of the wipe tower is no longer get emitted.
  
  - Fix the bug with part cooling fan speed being stuck at random values midway through the print.
  
  - Add the function to save z_offset baby-steps.

### v1.1 - Fixing problems with v1.0 and further testings

- Migrate the project files to Ondsel, the CAD software, and tighten up part-to-part tolerances

- Adds magnets to the docking system to hold onto the tool-head more securely when docked

- Increase wall thickness of the Tap&Change pieces, making it more durable

- Add door buffer, for clearance of the docked tool-heads.

- Add silicon liner layer for nozzle plug, to avoid PETG-caused damage.

- Passed reliability test with 4100 continuous tool-changes at random z-positions

- Adds support for the Nevermore StealthMax, with a modified flow chamber with output switch.

- User feedback. A design flaw has been discovered in the XLR Panels, which cause slight incompatibility with smaller Voron.

- Testing has shown that the better air flow control can significantly increase the utilisation of the bed heater for chamber heating.

- Multi-material experiments show that the tool-changer will benefit from chamber temperature management. Lower chamber temperature will allow ABS to be combined with PLA / PETG. However, the result is mixed, as many ABS print came out poorly due to the lower chamber temperature.

### v1.0 - First Beta

This is the first version of MissChanger for others to pick-up and build upon. Through testing, it shows the following pros:

- The tool-change mechanism is reliable (with ~5000 cycles on T0, thus far)

- The stock front z-motors can carry the weight of the dock and 4 tool-heads, ~2.5 kg

- The safety mechanism functions as intended, where the dock's Bar Ends will flex, before the dock are pushed into misalignment, before the front z-motors skip steps, before any damage is done. - This is in the event that the front gantry tilts down too far, causing the idlers to crash into the bottom corners of the dock.

- The umbilical does not get tangled until at least Z200, and printer is still functional up to Z250 with some limitation around the edge of the build area.

- The system can be toggled between single tool-head and multi-tool-heads mode without the use of any tool, in about 20-60s.

- Tool-change speed is relatively fast, ~8s

- Probe accuracy is very high, with `samples_tolerance: 0.00275` on all tool-head

- The Nudge calibration probe is very accurate and reliable

Nevertheless, the tests have also reveals the following cons:

- Tap&Change pieces are too fragile and would crack in the event of tool-head crash or with lower tolerance printed parts

- Incompatibility with GE5C bearing z mount for the Voron 2.4

- Incompatibility with front idler mods

- Tolerance for front gantry tilt is still too low

- Friction mounted tool-heads are susceptible to be bumped loose by door closing

- There are limits to the material combination in a tool changer, due to the shared chamber and bed temperatures

- The PTFE tube influences the curve of the umbilical more than everything else, beside the top panel

- Input shaper result is worse than that of the original Voron Tap

- This version was quick to be pushed to beta, because there was only one MissChanger in the work. Future versions will be given more time at each tier, as more people get on board with the project

### v0.0 - Original idea

* This was the original idea for MissChanger, which was developed up to the point where it can be used for test prints. It was discovered that the mechanism would wears down after ~2000 cycles and lost the precision needed for Quad Gantry Level.
  
  No further work will be done for this design, and documentations are not available.

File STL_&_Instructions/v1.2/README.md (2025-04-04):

# Table of content

1. [Introduction](#1-introduction) 

2. [Hardware](#2-hardware) 
   
   2.1. [MissChanger Core Assembly](#21-misschanger-core-assembly)
   
   2.2. [Situational / Optional / Mods](#22-situational--optional--mods) 

3. [Software](#2-software) 
   
   3.1. [Installation](#31-installation) 
   
   3.2. [Configuration](#32-configuration) 

4. [Calibration](#4-calibration) 
   
   4.0. [Tap&Change burn-in](#40-tapchange-burn-in) 
   
   4.1. [Park position calibration](#41-park-position-calibration) 
   
   4.2. [Input Shaper (optional)](#42-input-shaper-optional) 
   
   4.3. [Calibrate offsets](#43-calibrate-offsets) 

5. [Test and Troubleshoot](#5-test-and-troubleshoot) 
   
   5.1. [Offsets](#51-offsets) 

6. [Tool-change Tuning](#6-tool-change-tuning) 

7. [Slicer Profile](#7-slicer-profile) 

---

# 1. Introduction

Although the setting up the config for MissChanger will change some aspects of your printer, it is still recommended that you start the project with a functional printer with Voron-Tap, then add MissChanger and one tool-head at a time.

This document will not guide you through the set up of CAN bus or the physical mounting of the related hardware (i.e. U2C and tool-head board), please refer to the manufacture’s manual for that.

---

# 2. Hardware

## 2.1. MissChanger Core Assembly

The following manual is for the core components that are needed to get MissChanger up and running.

MissChanger Assembly Manual: [MissChanger_Assembly_Manual](./MissChanger_Assembly_Manual.pdf).

## 2.2. Situational / Optional / Mods

These following attachments are extras that will expand the capability of tool-changer system. Nevertheless, they were developed by others and does not share the same design language as MissChanger (i.e. difference print parameters).

| Mod | Description |
| --- | --- |
| [Nevermore Stealth Max](./6_Optionals/Nevermore_StealthMax)<br> + [DC Barrel Panel Mount](./6_Optionals/DC_Barrel_Panel_Mount) | - With modded flow chamber<br>- Cable management for Nevermore Stealth Max |
| [Galileo 2 + LDO Nitehawk SB USB cable strain relief](./5_Others/G2E-umbilical_anchor) | For Galileo 2 + LDO Nitehawk SB USB |
| [Inverted z-chain](https://www.printables.com/model/445298-inverted-z-chain-for-voron) | Recommended for the Voron 2.4 300mm, or smaller. To clear the space in front of the back gantry extrusion for the umbilicals. |

---

# 3. Software

This section aims to provide a guide through the installation process of the software and setup the config.

## 3.1. Installation

To install the [klipper-toolchanger](https://github.com/VIN-y/klipper-toolchanger) plugin, run the following installation script using the following command over SSH. This script will download this GitHub repository to your RaspberryPi home directory, and symlink the files in the Klipper extra folder.

Before installation. For those who are switching branch. You will need to run the following commands to clean out the old files before installing. Alternatively, you can run the uninstall script in below, in **section 3.1.2**.

```
cd ~
rm -rf klipper-toolchanger/
```

### 3.1.1. Install

1. For normal use: (TBD, intentionally broken command)

```
wget -O - https://raw.githubusercontent.com/VIN-y/klipper-toolchanger/main/scripts/install.sh | bash
```

2. For Beta test:

```
wget -O - https://raw.githubusercontent.com/VIN-y/klipper-toolchanger/beta/scripts/install.sh | bash
```

3. For Alpha test:

```
wget -O - https://raw.githubusercontent.com/VIN-y/klipper-toolchanger/alpha/scripts/install.sh | bash
```

*Note 1: You will need a `FIRMWARE_RESTART` whenever there is an update for the add-on.*

### 3.1.2. Uninstall

Some manual change will still need to be done in the user space (i.e. the section that is accessible via the web interface). This includes:

* The `config` folder

* The `misschanger_settings.cfg` file

* Irrelevant tool-head config file

* Irrelevant settings in `printer.cfg`

* `moonraker.conf` registry

These settings / files / folders tend to contain information and calibration values specific to your printer. Thus, it advised that you create a backup before deletion.

To fully uninstall the back-end, run one of the following command over SSH. Make sure to select the link that is relevant to the version that is currently install on the printer.

1. For normal use: (TBD, intentionally broken command)

```
wget -O - https://raw.githubusercontent.com/VIN-y/klipper-toolchanger/main/scripts/uninstall.sh | bash
```

2. For Beta test:

```
wget -O - https://raw.githubusercontent.com/VIN-y/klipper-toolchanger/beta/scripts/uninstall.sh | bash
```

3. For Alpha test:

```
wget -O - https://raw.githubusercontent.com/VIN-y/klipper-toolchanger/alpha/scripts/uninstall.sh | bash
```

## 3.2. Configuration

The **sample configuration files** can be found in the [Klipper_Config](./Klipper_Config) folder, where further descriptions of the software stack can also be found.

If you are comfortable with it, you are welcome to by-pass the default macros and play with the configs files to your liking, following **step -1**. If you found any errors or room  for improvement, feel free to reach out to me to get it fixed, via a GitHub or otherwise.

Nevertheless, the following are the recommended steps to get the software up-and-running using the default set of macros. Following the guide (starting from **step 1**) bellow will make it easier for you to get support. The default macros will be managed and updated together with the software stack.

### Step -1: Customisation

For building your custom macro:

1. Check where the relevant macro is saved, using the [code stack breakdown](./code_stack_breakdown.pdf) 

2. Download the relevant macro config file, in the [klipper-toolchanger](https://github.com/VIN-y/klipper-toolchanger/tree/main/macros) repository (or straight from your web interface)

3. Imported the config file back using the web interface

4. `inlcuded` it back into **printer.cfg** 

5. Comment-out (or delete) the reference to the file that the new config replaces, in **printer.cfg**

6. Save and Restart

7. Start editing the file to your liking

### Step 1: Back-up your running system

Through your web interface:

1. Select all of your config files

2. Download it to your computer

### Step 2: Set up printer.cfg

You can check the sample **printer.cfg** in [Klipper_Config](./Klipper_Config) folder as reference. However, be careful of copy-paste directly from there, because there are variables that might incompatible with yours printer. The following code blocks will intentionally have all optional functionalities (i.e. nozzle cleaning, active chamber thermal control, exhaust fans, etc.)

1. `includes` the following at the start of the **printer.cfg** file.

```
## Linked default marcros
[include misschanger_macros/config_switch.cfg]
[include misschanger_macros/homing.cfg]
[include misschanger_macros/nozzle_clean.cfg]
[include misschanger_macros/overwrite.cfg]
[include misschanger_macros/print_time_default.cfg]
[include misschanger_macros/tool_calibrate.cfg]
[include misschanger_macros/toolchanger.cfg]
## misschanger settings
[include misschanger_settings.cfg]
```

Optional:

```
[include misschanger_macros/tool_calibrate_extra.cfg]    # For the Nudge probe
```

2. Add **Global Variables**.

Each variable has been given a short description on what they do and some variable can be used to disable functionalities, such that you will not need to comb through the configs to find and edit them out.

```
####################################################################################
##                             Global Variables
####################################################################################
[config_switch]
#--------------------------------------------------------------------
[gcode_macro _static_variable]
description: Global static variables that is used through out the configs
## Tool-head calibration
variable_calibration_probe_x: 242.237500     # X aproximate position of the Nudge probe. CHANGE TO MATCH YOUR SET-UP
variable_calibration_probe_y: 329.825000     # Y aproximate position of the Nudge probe. CHANGE TO MATCH YOUR SET-UP
variable_calibration_safe_z: 60.00           # Z aproximate safe position of the Nudge probe. KEEP CONSERVATIVE TO AVOID COLLISION
variable_calibration_min_z: 40.00            # Z aproximate probe position of the Nudge probe.
variable_calibration_abs_z_seperately: 0     # "0" = False / "1" = True. For, the Nudge probe this should be '1'
variable_final_lift_z: 3                     # This must be the same as "final_lift_z" in [tools_calibrate] in misschanger_settings.cfg
## Cleaning dock
variable_clean_dock_x: 0                     # X aproximate position of the cleaning dock. CHANGE TO MATCH YOUR SET-UP. Set to "0" to disable
variable_clean_temp: 200                     # Nozzle clean temperature
variable_clean_threshold: 125.0              # The minimum perimeter of the print, below which the printing material will not be considered
## Always on crash detection
variable_alway_on_crash_detection: 1         # "0" = False / "1" = True
## For heatsoak macro
variable_heatsoak_temp: 0                    # Chamber temperature target for heat soak. REQUIRES [temperature_sensor Chamber] below. Set to "0" to disable
## Dynamic thermal expansion compensation
variable_thermo_expand_offset: -0.080        # Maximum z offset for thermal expansion compensation. REQUIRES [temperature_sensor Chamber] below
variable_thermo_expand_temp_high: 70         # Chamber temp to apply maximum z offset for thermal expansion compensation. REQUIRES [temperature_sensor Chamber]
variable_thermo_expand_temp_low: 0           # Chamber temp start applying thermal expansion compensation. REQUIRES [temperature_sensor Chamber]. Set to "0" to disable
gcode:                                       # This is here to appease klipper
```

3. Add the **Section Variables** section.

These sections need to be placed just before the **SAVE_CONFIG** section, as shown in the sample **printer.cfg**. Everything below the `Section Variable marker` will be swap in and out upon `A_CONFIG_TOGGLE`.

If a function settings were already existing somewhere else, the old function will need to be removed, or transfer to the new location. The critical settings that needs to be changed are as follow:

- `[quad_gantry_level]`, increase the y position of the front 2 `points:` to `130`, as shown, to avoid crashing into the dock.
- `[bed_mesh]`, make sure that `mesh_min: 30,130` , as shown, to avoid crashing into the dock.
- `[gcode_macro _home]` need to adjusted with the appropriate `xh` and `yh` which represent the centre of the built area.
- `variable_dock` is the indicator of which config is being used, is to be toggled in and out. 

```
####################################################################################
##                          Session Variables
####################################################################################
#;<    # Section Variable marker
#---------------------------------------------------------------
[include ./T0-SB2209-Revo-LDO.cfg]
[include ./T1-SB2209-Revo-LDO.cfg]
[include ./T2-Nitehawk-Revo-G2E.cfg]
[include ./T3-Nitehawk-Revo-LDO.cfg]
#---------------------------------------------------------------
[gcode_macro _home]
variable_xh: 175.0
variable_yh: 235.0
variable_safe_z: 60.0
# Dock is installed: True or False
variable_dock: True
gcode:
#---------------------------------------------------------------
[bed_mesh]
speed: 200                   # Calibration speed
horizontal_move_z: 10        # Z-axis movement speed
mesh_min: 30,130             # Minimum calibration point coordinates x, y
mesh_max: 320, 320           # Maximum calibration point coordinates x, y. 350mm=320,320
probe_count: 11,11           # Number of sampling points (7X7 is 49 points)
mesh_pps: 2,2                # Number of supplementary sampling points
algorithm: bicubic           # algorithmic model
bicubic_tension: 0.2         # Algorithmic interpolation don't move
#---------------------------------------------------------------
[quad_gantry_level]
#    Gantry Corners for 350mm Build
gantry_corners:
    -60,-10
    410,420
#  Probe points for 350mm Build
points:
    50,130
    50,300
    300,300
    300,130

speed: 150                   # Levelling speed
horizontal_move_z: 15        # Z-axis starting height
retries: 10                  # Number of out-of-tolerance retries
retry_tolerance: 0.0075      # Sampling tolerance
max_adjust: 20               # Maximum adjustment stroke for levelling
```

4. If it exist in **printer.cfg**, disable `[safe_z_home]` (comment-out or delete)

5. Add relevant variable (see the code snippet below) under **SAVE_CONFIG**. `[tool_probe T0]` and  `[extruder]` is needed no matter what your setup is. As, it is the reference / default tool-head. For each additional tool-head, you will need an associated set of  `[tool t(x)]`, `[tool_probe T(x)]`, and `[extruder(x)]`. **It is recommended** to add and test the tool-head, one at a time.

*NOTE 1: Your printer will be throwing error beyond this point, until the software is fully setup.* 

*NOTE 2: The variables in this section will need to be calibrated to match your hardware.* 

```
#*# [tool_probe T0]
#*# z_offset = -0.600000
#*#
#*# [extruder]
#*# control = pid
#*# pid_kp = 35.987
#*# pid_ki = 4.284
#*# pid_kd = 75.574
#*#
#*# [tool T1]
#*# gcode_x_offset = 0.259375
#*# gcode_y_offset = 0.256250
#*# gcode_z_offset = 0.490000
#*#
#*# [tool_probe T1]
#*# z_offset = -0.738
#*#
#*# [extruder1]
#*# control = pid
#*# pid_kp = 33.912
#*# pid_ki = 3.325
#*# pid_kd = 86.477
#*#
#*# [tool T2]
#*# gcode_x_offset = 0.087500
#*# gcode_y_offset = 0.912500
#*# gcode_z_offset = 0.207500
#*#
#*# [tool_probe T2]
#*# z_offset = -1.173
#*#
#*# [extruder2]
#*# control = pid
#*# pid_kp = 27.329
#*# pid_ki = 1.804
#*# pid_kd = 103.505
#*#
#*# [tool T3]
#*# gcode_x_offset = 0.156250
#*# gcode_y_offset = 0.925000
#*# gcode_z_offset = 0.080000
#*#
#*# [tool_probe T3]
#*# z_offset = -1.2105
#*#
#*# [extruder3]
#*# control = pid
#*# pid_kp = 34.630
#*# pid_ki = 3.785
#*# pid_kd = 79.217
```

### Step 3: Make the reference tool-head config file

Use the `T0-SB2209-Revo-LDO.cfg` as references.

1. Transfer the items relating to the tool-head from your `printer.cfg` to a separate file:
   
   * `[mcu EBBCan0]` - the MCU for your tool-head, named to your liking, i.e. EBBCan0.
   
   * `[adxl345]` - The accelerometer on the tool-head.
   
   * `[resonance_tester]` 
   
   * `[temperature_sensor]`
   
   * `[extruder]`
   
   * `[tmc2209]` - that is associated extruder motor
   
   * `[verify_heater]`
   
   * `[heater_fan]`
   
   * `[neopixel]` - if applicable
   
   * `[tool_probe]` 
     
     * <mark>!!!NOTE!!!</mark> that the `activate_gcode:` for the item has been replace with the macro `_TAP_PROBE_ACTIVATE`, with the flag `HEATER=extruder`. This flag <mark>NEED TO BE SET TO THE RIGHT "EXTRUDER"</mark>. Failure to do so, may result in damage bed surface.

2. Replace `[fan]` with `[fan_generic T0_partfan]`

3. Add the following item and macro:
   
   * `[gcode_macro T0]` - for tool switching
   
   * `[tool T0]` - associate the items above to T0 and provide tool specific variables (which will need to be adjusted later).

4. Include tool-head config in the session variables are in `printer.cfg`, as shown in the code block in **Step 2.3**.

*Note: At this point, the printer should be able to have a firmware restart without (or with minor) errors.* 

### Step 5: Calibrate and test T0

1. Remove the dock and any attached tool-head other than T0 (for safety reason).

2. Run `FIRMWARE_RESTART`, and fix any problem that arise ;)

3. Run `G28` and `QUAD_GANTRY_LEVEL` 

4. Check that:
   
   * The printer home Y before X
   
   * Quad gantry level front points are at Y130
   
   * Extruder PID is correctly set and applied (no error / no bouncing temperature)

5. Re-mount the dock

6. Calibrate extruder `rotation_distance`

7. Calibrate heater PID

8. Calibrate the park position, see **section 4.1.** 

9. Calibrate the `z_offset`, see **section 4.3.** 

10. (optional) Calibrate input shaper, see **section 4.2.** 

11. Save & Restart

### Step 6: Make the next tool-head and its config file

1. Follow the hardware assembly guide from the manufacture of the relevant hardware, i.e extruder, tool-head board, etc.

2. Mount the dock and temporary mount the new tool-head to the dock.
   
   <mark>CAUTION:</mark> **DO NOT** try to make the print pick up the tool yet.

3. Use `T1-SB2209-Revo-LDO.cfg` (and others) config file as references. Make, calibrate, and test the config files for the other tool-heads.

4. Include tool-head config in the session variables are in `printer.cfg`, as shown in the code block in **step 2.3**.

5. Copy and paste the associated set of `[tool t(x)]`, `[tool_probe T(x)]`, and `[extruder(x)]` to the **SAVE_CONFIG** section, if they are not already there.

6. Save & Restart

### Step 7: Calibrate and test tool-head

If this is the first tool-head you made beside the reference tool-head. Then you will need to test the max available y of your set up:

1. Run `G28`

2. Manually nudge the tool-head to right behind a docked tool (via the web interface), but not touching

3. Note down the Y position of that location

4. If the y location is greater than 120 mm, then you will need to update the `params_safe_y` in `[toolchanger]` in `misschanger_settings.cfg`

5. Save & Restart

Otherwise:

1. Calibrate extruder `rotation_distance`

2- Calibrate heater PID

3. Save & Restart

4. Run `G28` and `QUAD_GANTRY_LEVEL`

5. Calibrate the park position, see **section 4.1.** 

6. Calibrate the `z_offset`, see **section 4.3.** 

7. (optional) Calibrate input shaper, see **section 4.2.** 

### Step 8: Other macros

* `macro-general.cfg`

* `macro-test.cfg`

These configs tends to be points of customisation for many. Therefore, the included files are intended to be inspirations for your own macros. They contains commands and functionalities that may not be needed or are relevant to your printer.

### Step 9: Single tool-head config

1. Run `SAVE_CONFIG_MODE` to save the current setup.

2. Check if the save was made correctly, in the **config** folder.

3. In the Section Variable section in **printer.cfg**:
   
   1. Comment out all included tool-head configs other than T0
   
   2. Under `[gcode_macro _home]`:
      
      1. Set an appropriate `xh` and `yh` which represent the centre of the new built area.
      
      2. Set `variable_dock` to `False`
   
   3. Revert to `[bed_mesh]` and `[quad_gantry_level]` to the original values of the stock machine (without the tool-changer bits)
   
   4. Delete the all `[tool T(x)]`, `[tool_probe T(x)]`, and `[extruder(x)]` under the `SAVE_CONFIG` section. EXCEPT: `[tool_probe T0]` and `[extruder]`.

4. Save, but no restart is needed.

5. Run `SAVE_CONFIG_MODE` and check if the file is correctly saved.

Now, the `CONFIG_TOGGLE` macro will allow you to toggle between these 2 configs.

---

# 4. Calibration

This section assumes that the new tool-head has been assembled, wired up, and has been recognised by Klipper.

## 4.0. Tap&Change burn-in

The following steps are for the burn-in of the Tap&Change mechanism. This is so that it can sort out any misalignment due to print tolerance and assembly. Through testing, it has been shown that this only need to be done once for every Tap&Change rail-side (there is only one in the system).

1. Setup to the variable for `SHAPER_CALIBRATE`, to your liking

2. Manually mount T0

3. Run `G28`

4. Bring the tool-head to 10 mm above the centre of the bed

5. Turn on the bed heater

6. Turn on the chamber fan (if exist)

7. Wait until the tool-head (i.e. "Extruder") temperature reached ~40°C (or ~10 mins if you don't have a chamber temperature sensor)

8. Run `SHAPER_CALIBRATE` - Note: This is only meant to shake the tool-head around in its mount. Do not save the input shaper result.

9. Repeat step 4 - 8 until, the tool-head can fall into the mount on it's own weight.

## 4.1. Park position calibration

1. Run `G28` and `QUAD_GANTRY_LEVEL`  - if not already done

2. Run `G1 Z150 F9000` 

3. Run `STOP_TOOL_PROBE_CRASH_DETECTION` 

4. Loosen the bolts on the bottom of the dock of the relevant dock (so it will spin around the bar)

5. On the web interface, in `Setting > Control` add `0.1` and remove `100` in the `Move distance increments X & Y axes (in mm)` 
   
   *Note: This is temporary for this step only, and can be reverted later.*

6. Set the dock at the empty position, i.e. at the bottom of the ramp.
   

7. Use the web interface, nudge the tool-head into the correct x-position. This can be tested by nudging the y-position in and out to see which side of the tool-head touch the dock first. Then adjusts it, such that both side of the dock would touch the tool-head at the same time.
   

8. Copy and paste the current x-coordinate into the `params_park_x:` of the config file of the current tool-head

9. Save it, **BUT DON'T RESTART**

10. Nudge the y-position until the dock until the dock is fully seated.
    
    1. Make sure that the whole dock-bar is not lifted.
    
    2. Make sure the tool-head is fully seated before it starts being lifted. Check it by nudging it back and fort 10mm.
    
    3. If step 10.i and 10.ii is not met. Adjust the Bar Ends spacers to fit. TIP: the distance for the spacers should be the same for both side.

11. Tighten the bolts on the bottom of the dock (locking it in place)

12. Nudge the y-position until the dock is at the peak of the ramp. The dock is tough enough to handle a bit of pressure from the gantry. So you can keep nudging the y-position until the dock flex a bit, then back it off.

13. Run:
    
    ```
    G91
    G1 Y+80 F6000
    G90
    ```

14. Copy and paste the current y-coordinate into the `params_park_y:` of the config file of the current tool-head

15. Save it

16. Run `FIRMWARE_RESTART`

17. Run the `TEST_DOCKING` macro

## 4.2. Input Shaper (optional)

*Note: To avoid Klipper from throwing errors, the parameters for input shaper are pre-populated in* `toolchanger.cfg` *and in each tool-head config files. Nevertheless, it is best to calibrate it for each available tool-head.*

1. Enable (un-comment) the `[adxl345]` and `[resonance_tester]` in the config of the tool-head that is to be calibrated

2. Disable (comment out) the `[adxl345]` and `[resonance_tester]` in the config of the other tool-heads

3. Save & Restart

4. Mount the tool-head that is to be calibrated

5. Run `G28` and `QUAD_GANTRY_LEVEL`

6. Run `SHAPER_CALIBRATE` - **BUT, DO NOT SAVE**

7. From the console output, save the following parameters into the tool-head config (at the bottom of the `[tool Tx]` section)
   
   ```
   params_input_shaper_type_x: ...
   params_input_shaper_freq_x: ...
   params_input_shaper_damping_ratio_x: ...
   params_input_shaper_type_y: ...
   params_input_shaper_freq_y: ...
   params_input_shaper_damping_ratio_y: ...
   ```

8. Save & Restart

## 4.3. Calibrate offsets

### 4.3.1. Calibrate reference z-offset

1. Mount tool-head T0

2. Go to T0 config file. Make sure:
   
   - `z_offset` under `[tool_probe T0]` is commented out
   
   - Every other offsets to `0`; i.e. `x_offset` and `y_offset`
   
   - Save it, **BUT DON'T RESTART** 

3. Run `G28` and `QUAD_GANTRY_LEVEL` 

4. Run `PROBE_CALIBRATE` on the console and go through the process with <u>the normal paper test</u>.

5. <u></u>Run `SAVE_CONFIG` - which will restart your printer

6. Go to `printer.cfg`

7. Copy the z-offset value from:
   
   ```
   #*# [tool_probe_endstop]
   #*# z_offset = {value}
   ```
   
   And, paste it to:
   
   ```
   #*# [tool_probe T0]
   #*# z_offset = {value}
   ```

8. Delete:
   
   ```
   #*# [tool_probe_endstop]
   #*# z_offset = {value}
   ```
   
   *Note: It will not be used regardless of whether it is there or not.*

9. Save & Restart

*Note: It is key that you get the z_offset correct for the T0, as it will be used to extrapolate other offsets later on. Therefore, it is worth diverge from the instruction, if you have a preferred way to set your the z-offset.*

### 4.3.2. Calibration probe setup

At this stage, you should have:

- The calibration probe assembled, tested, and installed

- T0 z-offset calibrated

This section will guide you through the calibration of the machine specific variable `trigger_to_bottom_z`, which will allow you to automate the z-offset of the tool-heads that are not T0.

*Note: This should be your go to variable to adjust whenever you ran into z-offset issue.*

### Setup:

1. Open `misschanger_settings.cfg`

2. Setup `[tools_calibrate]` with the correct `pin`

3. Save and restart

4. Open `printer.cfg` 

5. Set the approximate X and Y location of the Nudge pin in `[gcode_macro _static_variable]` 

6. Save and restart

### Steps:

1. Go to `printer.cfg` and record the `z-offset` for `[tool_probe T0]`, which should be at (or near) the bottom of the file

2. Mount tool-head **T0** and make sure it's nozzle is clean

3. Run `G28` and `QUAD_GANTRY_LEVEL`

4. Mount the calibration probe

5. Run `CALIBRATE_TRIGGER_BOTTOM`. If it is a fresh calibration probe, it is worth redoing this step until the suggested value is consistent at +/- 0.005mm. 

6. Copy the proposed offset on the console to the `trigger_to_bottom_z:` in `[tools_calibrate]`.

7. Save and restart

8. Run `CALIBRATE_OFFSETS TOOL=0` - But, **DON'T RESTART**

9. Check if proposed z-offset to be +-0.01mm of the recorded `z_offset` in **step 1**.

10. Run `CALIBRATE_OFFSETS TOOL=0` 2-3 more times to make sure the measured value is consistence.

Your calibration probe is ready.

*Note: It is worth mentions that there are other ways to calibrate your offsets, such as the visual based solution from [Ember](https://www.emberprototypes.com/products/cxc) or the calibration print that you can get from [Printables](https://www.printables.com/model/201707-x-y-and-z-calibration-tool-for-idex-dual-extruder-). Each with their pros and cons, in term of accuracy and cost. However,  a physical contact probe is currently the only way to automatically calibrate all relevant offsets.*

### 4.3.3. Other tool-head(s)

### Steps:

1. <mark>**!!! MAKE SURE THE CALIBRATION PROBE IS NOT MOUNTED !!!**</mark>

2. Make sure all tool-heads are cold (near room temperature)

3. Make sure all nozzles are clean

4. Make sure all tool-head config file (except T0) has the following variable disabled (commented out):
   
   - `gcode_x_offset` 
   
   - `gcode_y_offset` 
   
   - `gcode_z_offset` 
   
   - `z_offset` 

5. Save it, **BUT DON'T RESTART**

6. Mount tool-head T0

7. Run `G28` and `QUAD_GANTRY_LEVEL`

8. Mount the Nudge probe

9. Run `CALIBRATE_OFFSETS` - the process is automatic, but you can specify a specific tool-head

10. Run `SAVE_CONFIG`

If you has the set `variable_calibration_abs_z_seperately` to `1` in `[gcode_macro _static_variable]` in **printer.cfg** (for the Nudge probe).

1. Mount tool-head T0

2. Run `G28` and `QUAD_GANTRY_LEVEL` 

3. Run `CALIBRATE_ABSOLUTE_Z` 

4. Run `SAVE_CONFIG`

### 4.3.4. Clean dock

#### Steps:

1. Install the clean dock in your prefer slot on the gantry

2. Approximate the x position of the centre of the dock (where the brush is)

3. Add the aforementioned x position into `printer.cfg`. In `variable_clean_dock_x` under `[gcode_macro _static_variable]`.

#### Optional steps, for auto mid-print clean:

1. Set-up the `variable_clean_threshold` under `[gcode_macro _static_variable]`. "150" means that the print need to take up ~50% of the bed before trigger mid-clean print.

2. List the materials that need to have their associated tool-head cleaned in `misschanger_settings.cfg`. For example:
   
   ```
   params_need_clean_materials: ['PETG', 'FLEX']
   ```

---

# 5. Test and Troubleshoot

## 5.1. Offsets

It is important to test if the `z_offset` and `gcode_z_offset` are set-up and applied correctly. A miss-configured `z_offset`/`gcode_z_offset` can cause the nozzle to be dragged on the bed, risking damage. Please follow the steps below to test the config, before you start printing.

### Part 1: Check the z_offset of T0

1. Make sure the printer is cold (near ambient temperature).

2. Run `G28` and `QUAD_GANTRY_LEVEL` with T0

3. Run `G1 X175 Y235 Z10 F9000` (centre of print area)

4. Run `G1 Z0 F9000` 

5. Test the z-offset with the paper test. - If it is good then you set-up `trigger_to_bottom_z` correctly.

6. If it does not work:
   
   1. baby step the z position to correction.
   
   2. adjust `trigger_to_bottom_z` accordingly using the baby stepped amount.
   
   3. then, rerun `CALIBRATE_OFFSETS TOOL=0`.
   
   4. retry step 1 to 4.

### Part 2: Check the gcode_z_offset of the other tools

1. Goes through step 1 and 2 of part 1, above.

2. Switch to next tool, via the web UI or Klipper Screen.

3. Goes through step 3 to 6 of part 1, above.

4. If it does not work. rerun `CALIBRATE_OFFSETS TOOL=[x]` for that tool-head (or all of them).

### Part 3: gcode_x_offset and gcode_y_offset

To validate `gcode_x_offset` and `gcode_y_offset`, you just need to print something and see if they are set-up and applied correctly. Alternatively, you can also buy and use [Ember Camera Assisted XY](https://www.emberprototypes.com/products/cxc) to validate them.

---

# 6. Tool-change Tuning

The speed and path of the default tool-change routine, in `misschanger_settings.cfg` is not tuned for reliability. It is slower and has more steps than needed.

For a smooth running MissChanger. The `params_path_speed` can be increased and some of the "Wiggle wiggle", in the path, can be disable. For example:



---

# 7. Slicer Profile

## Custom Start G-code

Copy and paste the following code into your slicer.

*Note: It need to stay as a single line of gcode.*

```
PRINT_START BED_TEMP=[first_layer_bed_temperature] FIRST_LAYER_PRINT_SIZE=[first_layer_print_size] FIRST_LAYER_HEIGHT=[first_layer_height] TOOL=[initial_tool] TOOL_TEMP={first_layer_temperature[initial_tool]} {if is_extruder_used[0]}T0_TEMP={first_layer_temperature[0]} T0_Fil={filament_type[0]}{endif} {if is_extruder_used[1]}T1_TEMP={first_layer_temperature[1]} T1_Fil={filament_type[1]}{endif} {if is_extruder_used[2]}T2_TEMP={first_layer_temperature[2]} T2_Fil={filament_type[2]}{endif} {if is_extruder_used[3]}T3_TEMP={first_layer_temperature[3]} T3_Fil={filament_type[3]}{endif}
```



Also. Disable the following option:



## Slicer Bed Shape

The printer bed shape need to be set as shown below, to avoid collisions with the dock during printing.

Depending on the umbilical mounting solution on the tool-head side, the lost y can be between 120mm to 140mm.

*Note: It can be seen here that the max print height was set to 235mm. This is recommended for new machines to avoid umbilical tangling. However, if you are willing to do some tuning to the tension of the umbilical or add a top hat to the system, the max print height can be increased to 250mm or 300mm.*

### For printers with 350mm beds:



### For printers with 300mm beds:



## Multiple Extruder

Enable **Ooze Prevention**.

This setting will allow you to reduce the docked nozzle temperature, to prevent over cooking the filament.

Even if you don't want it to drop the temperature, still enable it, then set the `Temperature variation` to -25°C. This setting will emit a nozzle heating command after tool-change, effectively act as reheat command for when the system is recovering from a failed tool-change.



## Speed profile

Although, you might want to tune your own speed profile for the best performance. Here is a slow and reliable profile to get you started with.



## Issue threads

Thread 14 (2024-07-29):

Any idea how it could work with a  voron trident

a625013463, 2024-07-29:
Do you have any idea how it could work with a voron trident?

may be you have an idea and some kind of picture to show how :-)

thanks and greetings

VIN-y, 2024-07-29:
The Voron Trident use the same XY gantry as the 2.4 (it is just bolted in place); thus, the tool-change mechanism and dock should already works for it, without any modification needed. The bits that need to be changed are the XLR panels and the Nudge (calibration probe) mount.

In other words, it should be pretty easy to do. However, I can't afford (or have) a Trident to work with.

So... either:
1. Someone, who have a Trident, pick up that tab. (most likely... hopefully)
2. The project got popular enough and get noticed by someone who is willing to sent me a Trident. (better not get your hope up)
3. I save up the funds needed for a Trident. (early-mid 2025)

VIN-y, 2024-08-01:
Oh wait. I just check the Trident manual for the dimensions. The XLR panels should fit.

a625013463, 2024-08-06:
Thanks a lot, I own a Voron Trident and I'll go back and try it out, thanks again

Marck80, 2024-12-06:
Were you able to mount it on the Trident?

VIN-y, 2024-12-06:
@Marck80 At the bottom. Pretty much the same place where they would be on the 2.4.

VIN-y, 2024-12-09:
I got the chance to play with a couple of Trident at SMMRF2024. From which I got 2 observations:
1. The Nudge probe can be used with the Trident using the float base that is provided in the original repo. When you don't need it, you can just leave it to the side. Because the gantry doesn't go down, there is a lot of space to play with.
2. The XLR panels should work on the bigger Trident, 350. But, things will get dicey for smaller ones. As the z drag chain terminated where the foot of the panel is meant to stick out and be bolted to the extrusion at the back.

Marck80, 2024-12-11:
I just have the 300..I'll try to print and see if there are any problems..I'll let you know

Battlecake91, 2025-02-06:
Is there any update on this topic?

I'm building a Trident 350 with more on the Z axis (350x350x400) and I 100% want a toolchanger system for stealthburner (as I'm using a lot of adittional stuff there - so DAKSH isn't a good option for me).

I will try to integrate this system on my Trident, but if you saw some bigger problems, it could help me to save some time.

VIN-y, 2025-02-06:
> Is there any update on this topic?

We got some one who is building MissChanger on a Trident. From their feedback (which has been implemented to v1.2):
- The top bar of the dock has to be removed.

With that said, no further compatibility issue has been found thus far.

Nevertheless, I have decided to extend the alpha to see how that Trident build go. I cannot publicly give you a date on when it is ready, though. As is the nature of an open-source project (where time is donated), it is done when it is done.

VIN-y, 2025-02-06:
yes. I usually gave everyone a head-sup on discord whenever I about to do something.

VIN-y, 2025-03-24:
FYI.
Early tester has confirmed the need for a top-hat. The umbilical rubbing on the top panel will cause problems with probe accuracy.

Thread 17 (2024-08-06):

Tap&Change v1.0 problems

VIN-y, 2024-08-06:
1. The walls around the magnets are too thin. This leads to cracking along the layer line during installation or after a toolhead crash.

2. The interface between the Tap&Change and the Dock wears out over time, creating a loose docked state.

VIN-y, 2024-08-06:
This is being addressed in v1.1.

Closed 2024-09-16.

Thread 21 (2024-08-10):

Dock v1.0 problems

VIN-y, 2024-08-10:
Although it works, and is reliable, it can be seen that the toolhead can be bumped slightly out of position if the door is closed too quickly or twisted out of place if the umbilicals is set-up too tight or colliding with each others.

VIN-y, 2024-08-10:
This is being addressed in v1.1.

VIN-y, 2024-09-16:
N52 magnets have been added to the Docck a Tap&Change system to hold the tool-head in place.

Closed 2024-09-16.

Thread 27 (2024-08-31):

Nozzle plug degrades

VIN-y, 2024-08-31:
The oven liner used for the nozzle plug degrades overtime when printing with PETG.

Potential fix: silicon oven liner

VIN-y, 2024-09-16:
the Teflon liner is kept to hold everything in place. A layer of silicon over liner is added around the widen section of the Teflon, to provide resistances against PETG and add some pressure against the nozzle to prevent oozing.

Closed 2024-09-16.

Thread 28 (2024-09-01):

z-offset is not correctly saved

VIN-y, 2024-09-01:
when you click `SAVE_CONFIG` after baby stepping, the result is saved as:
```
#*# [tool_probe_endstop]
#*# z_offset = -0.647
```
which is wrong and not going to be used in to the system regardless.

It is good that the values does not overwrite or messed up other values if the accidental clicks were to happened. However, it would be nice to be able to retain the various way to save the baby step results.

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
VIN-y, 2024-09-01:
@goncastrum  I don't know how familiar with Github and all of that. Regardless, linking to some random with the most generic description there is, i.e.:

> to fix your trouble try this fix

is the best way to get reported and banned.

So explain yourself, before I do that.

iam-py-test, 2024-09-02:
@VIN-y they are a known spam bot. The MediaFire link downloads a password-protected archive containing an unknown piece of malware:
https://github.com/hagezi/dns-blocklists/issues/3598
https://www.virustotal.com/gui/file/1f79a95f6bde6c375a9d60dfba8c02fd463d2cbe1d2d7a38eaa0ba403d3529d0/detection
Thanks

VIN-y, 2024-09-12:
Interestingly. Different material prefers different z-offset on the same tool-head. So more work need to be done per tool-head after the calibration via the calibration probe. The Nudge probe works fantastically for multi-colour tool-changes.

VIN-y, 2024-09-12:
What I have been doing so far is to let the system safe the default (but is now irrelevant) variable `[tool_probe_endstop]`. Then manually go to `printer.cfg` to copy-paste the value to the correct section.

VIN-y, 2024-09-21:
Ultimately, I do not want to tamper with klipper's core functions. Therefore, as long as the issue is a tolerable one, no action will be done here.

Closed 2024-09-21.

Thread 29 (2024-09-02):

Prusa Slicer set the wrong temperature for prints in which only 1 tool is active

VIN-y, 2024-09-02:
Prusa Slicer generate the following code after `PRINT_START`, if the `Emit temperature command automatically` option is enabled for print with a single tool:
```
...
M109 S250
M109 S200
...
```

VIN-y, 2024-09-02:
The best solution I found thus far is to just disable the `Emit temperature command automatically` option, and manage the starting nozzle and bed temp within `PRINT_START`

Closed 2024-09-16.

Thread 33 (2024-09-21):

Chamber overheating

VIN-y, 2024-09-21:
When the door is closed, the chamber will naturally raised above ~40°C, causing heat creep for PETG and PLA. This leads to the printer being unable to combine ABS and other materials.

The solution for this is to have fan(s) to exhaust the hot air out off the printer. However, this is not ideal for ABS due to the smell and VOC. For it to work there must be a filter system for the exhausted air. The key question here is where do I put it? In addition, because the HEPA and carbon filter has specific shell life and needs to be replaced often; which filter should I go for?

Closed 2024-10-14.

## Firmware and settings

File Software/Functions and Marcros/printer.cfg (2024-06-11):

[include mainsail.cfg]
[include homing.cfg]
[include toolchanger.cfg]
[include calibrate-offsets.cfg]

[include ./macros/macro-general.cfg]
[include ./macros/macro-print.cfg]

# [include Settings_1_printer-single.cfg]

[include Settings_2_printer-multi.cfg]
[include ./macros/macro-tc-nozzle_clean.cfg]

[exclude_object]

####################################################################################
## 	                MCU
####################################################################################
[mcu]
serial: /dev/serial/by-id/usb-Klipper_stm32f446xx_0C0035001150535556323420-if00

####################################################################################
##                     Model and acceleration
####################################################################################
[printer]
kinematics: corexy           # Printer type：corexy
max_velocity: 300            # Maximum speed (max. 300)
max_accel: 5000              # Maximum acceleration (max. 4000)
max_z_velocity: 15           # Z-axis maximum speed
max_z_accel: 350             # Z-axis maximum acceleration
square_corner_velocity: 5.0  # Square corner speed

####################################################################################
##	                 Temperature Monitoring
####################################################################################
[temperature_sensor Chamber]
sensor_type: Generic 3950
sensor_pin: PF4

[temperature_sensor MCU]        
sensor_type: temperature_mcu

[temperature_sensor Ras-Pi]
sensor_type: temperature_host

####################################################################################
#   B(X) ---------A(Y)
#   |                |
#   |--------E-------|
#   |                |
#   |                |
#   |                |
####################################################################################
##                   X-axis on MOTOR_0(B Motor)
####################################################################################
[stepper_x]
step_pin: PF13                # X-axis motor pulse pin setting
dir_pin: !PF12                # X-axis motor direction pin setting
enable_pin: !PF14             # X-axis motor enable pin setting
microsteps: 32                # Motor microsteps Setting
rotation_distance: 40         # Active pulley circumference mm (2GT-20T pulley 40, 2GT-16T pulley 32)
full_steps_per_rotation:200   # Number of pulses required for a single motor revolution (1.8 degree motor: 200, 0.9 degree motor: 400)
endstop_pin: PG6              # PG6           # Limit switch PIN pin setting（X-）
position_min: 0               # X-axis minimum travel - software limit
position_endstop: 350         # Mechanical reset point coordinates for X-axis (change to 350 for 350 models)
position_max: 350             # X-axis maximum travel - software limit (change to 350 for 350 models)
homing_speed: 50              # Reset speed maximum 100
homing_retract_dist: 5        # Setback distance after the first trigger of the reset switch
homing_positive_dir: true     # Direction of reset (generally no change required)

[tmc2240 stepper_x]
cs_pin: PC4
spi_software_sclk_pin: PA5
spi_software_mosi_pin: PA7
spi_software_miso_pin: PA6
driver_TPFD: 0
run_current: 0.8

####################################################################################
##                   Y-axis on MOTOR_1(A Motor)
####################################################################################

[stepper_y]
step_pin: PG0                 # Y-axis motor pulse pin setting
dir_pin: !PG1                 # Y-axis motor direction pin setting
enable_pin: !PF15             # Y-axis motor enable pin setting
microsteps: 32                # Motor microsteps Setting
rotation_distance: 40         # Active pulley circumference mm (2GT-20T pulley 40, 2GT-16T pulley 32)
full_steps_per_rotation:200   # Number of pulses required for a single motor revolution (1.8 degree motor: 200, 0.9 degree motor: 400)
endstop_pin: PG9              # Limit switch PIN pin setting（Y-）
position_min: 0               # Y-axis minimum travel - software limit
position_endstop: 350         # Mechanical reset point coordinates for Y-axis (change to 350 for 350 models)
position_max: 350             # Y-axis maximum travel - software limit (change to 350 for 350 models)
homing_speed: 50              # Reset speed maximum 100
homing_retract_dist: 5        # Setback distance after the first trigger of the reset switch
homing_positive_dir: true     # Direction of reset (generally no change required)

[tmc2240 stepper_y]
cs_pin: PD11
spi_software_sclk_pin: PA5
spi_software_mosi_pin: PA7
spi_software_miso_pin: PA6
driver_TPFD: 0
run_current: 0.8

####################################################################################
#   z1 -------------- z2
#   |                 |
#   |                 |
#   |                 |
#   |                 |
#  z0---   display ---z3
####################################################################################
##                  Z0-axis
####################################################################################
##		Z0-axis on MOTOR2_1(left front)
[stepper_z]
step_pin: PF11    		                # Z-axis motor pulse pin
dir_pin: !PG3                           # Z-axis motor direction pin setting
enable_pin: !PG5                        # Z-axis motor enable pin setting
rotation_distance: 40                   # Active pulley circumference mm (2GT-20T pulley 40, 2GT-16T pulley 32)
gear_ratio: 80:16                       # reduction ratio
microsteps: 16                          # microsteps
endstop_pin: probe:z_virtual_endstop    # PG10          # Limit switch interface

##  position_endstop is the distance of the Z limit pin trigger point from the print surface.
##  Positive value = above the termination point of the platform，
##  Negative value = termination point below the plateau.
##  Increasing the value of position_ endstop will bring the nozzle closer to the bed.
##  After running Z_ENDSTOP_CALIBRATE, position_endstop will be stored at the end of the CFG configuration.
##  position_endstop: 0.5      # Modified as per actual
position_max: 330              # Maximum Z-axis print height  #350mm=330
position_min: -5               # Soft Limit Minimum Stroke
homing_speed: 10               # Reset speed - maximum 20
second_homing_speed: 3         # Secondary reset speed - maximum 10
homing_retract_dist: 3         # Retreat distance
#--------------------------------------------------------------------
[tmc2209 stepper_z]        # TMC2209
uart_pin: PC6              # drive communications port
interpolate: true          # Whether to enable 256 microstep interpolation
run_current: 0.8           # Motor running current value(mA)
hold_current: 0.8          # holding current(mA)
sense_resistor: 0.110      # Do not change the drive sampling resistor
stealthchop_threshold: 200 # Mute threshold

#--------------------------------------------------------------------#
##		Z1-axis on MOTOR3(left rear)
[stepper_z1]
step_pin: PG4              # Z1-axis motor pulse pin
dir_pin: PC1               # Z1-axis motor direction pin setting
enable_pin: !PA0           # Z1-axis motor enable pin setting
rotation_distance: 40      # Active pulley circumference mm (2GT-20T pulley 40, 2GT-16T pulley 32)
gear_ratio: 80:16          # reduction ratio
microsteps: 16             # microsteps
#--------------------------------------------------------------------
[tmc2209 stepper_z1]       # TMC2209
uart_pin: PC7              # drive communications port
interpolate: true          # Whether to enable 256 microstep interpolation
run_current: 0.8           # Motor running current value(mA)
hold_current: 0.8          # holding current(mA)
sense_resistor: 0.110      # Do not change the drive sampling resistor
stealthchop_threshold: 200 # Mute threshold

#--------------------------------------------------------------------#
##		Z2-axis on MOTOR4(right-rear)
[stepper_z2]
step_pin: PF9              # Z2-axis motor pulse pin
dir_pin: !PF10              # Z2-axis motor direction pin setting
enable_pin: !PG2           # Z2-axis motor enable pin setting
rotation_distance: 40      # Active pulley circumference mm (2GT-20T pulley 40, 2GT-16T pulley 32)
gear_ratio: 80:16          # reduction ratio
microsteps: 16             # microsteps
#--------------------------------------------------------------------
[tmc2209 stepper_z2]       # TMC2209
uart_pin: PF2              # drive communications port
interpolate: true          # Whether to enable 256 microstep interpolation
run_current: 0.8           # Motor running current value(mA)
hold_current: 0.8          # holding current(mA)
sense_resistor: 0.110      # Do not change the drive sampling resistor
stealthchop_threshold: 200 # Mute threshold
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

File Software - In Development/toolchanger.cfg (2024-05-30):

[rounded_path]
resolution: 0.2
replace_g0: True

[tool_probe_endstop]
crash_gcode:
    RESPOND TYPE=error MSG='Tool not detected, expected {printer.toolchanger.tool_number}. Pausing the print.' 
    M84
    TURN_OFF_HEATERS

[tools_calibrate]
pin: ^!PF5
travel_speed: 20  # mms to travel sideways for XY probing
spread: 7  # mms to travel down from top for XY probing
lower_z: 1.0  # The speed (in mm/sec) to move tools down onto the probe
speed: 2  # The speed (in mm/sec) to retract between probes
lift_speed: 4  # Z Lift after probing done, should be greater than any Z variance between tools
final_lift_z: 6 
sample_retract_dist:2
samples_tolerance:0.05
samples:5
samples_result: median # median, average

[toolchanger]
t_command_restore_axis: Z
params_safe_y: 120
params_close_y: 50
params_min_z: 35
params_fast_speed: 10000 # Go as fast as we can
params_path_speed: 5000

params_type = 'sb_misschanger'
params_sb_misschanger_path: [
                             {'x':0,        'y':0,       'f':1.00},
                             {'x':0,        'y':-60,     'f':0.80},
                             {'x':0,        'y':-65,     'f':0.60},
                             {'x':0,        'y':-70,     'f':0.60},
                             {'x':0,        'y':-75,     'f':0.60},
                             {'x':0,        'y':-70,     'f':0.60},
                             {'x':0,        'y':-75,     'f':0.40},
                             {'x':0,        'y':-70,     'f':0.40},
                             {'x':0,        'y':-75,     'f':0.30},
                             {'x':0,        'y':-70,     'f':0.30},
                             {'x':0,        'y':-80,     'f':0.20},
                             {'x':-6.0,     'y':-80,     'f':0.20},  
                             {'x':-6.0,     'y':-70,     'f':0.30},
                             {'x':-6.0,     'y':-40,     'f':1.00}
                            ]

initialize_gcode:
    DETECT_ACTIVE_TOOL_PROBE
    _INITIALIZE_FROM_DETECTED_TOOL

before_change_gcode: 
    {% set tn = "T"+(tool.tool_number|string) %}
    {% if printer["gcode_macro " + tn ] %}
        SET_GCODE_VARIABLE MACRO={tn} VARIABLE=color VALUE="''"
    {% endif %}

after_change_gcode: 
    {% set tn = "T"+(tool.tool_number|string) %}
    {% if printer["gcode_macro " + tn ] %}
        SET_GCODE_VARIABLE MACRO={tn} VARIABLE=color VALUE="'c44'"
    {% endif %}    
    {% if tool.params_input_shaper_freq_x %}
        SET_INPUT_SHAPER SHAPER_FREQ_X={tool.params_input_shaper_freq_x} SHAPER_FREQ_Y={tool.params_input_shaper_freq_y}
    {% endif %}
    
dropoff_gcode:
    {% set x = tool.params_park_x|float %} 
    {% set y = tool.params_park_y|float %} 
    {% set z = tool.params_park_z|float %}
    {% set fast = tool.params_fast_speed|float %}
    {% set path = tool['params_' ~ tool.params_type ~ '_path'] %}
    {% set max_z = printer.configfile.config["stepper_z"]["position_max"]|float %}
    {% set cur_z = printer.toolhead.position[2]|float %}
    RESPOND TYPE=echo MSG='Dropping off {tool.name}'
    
    ##############  Clearance move    ##############
    # Move 1 mm up to avoid crashing into things, unless the it is lower than params_min_z
    G90
    {% if cur_z <= tool.params_min_z %}
        G0 Z{ tool.params_min_z+1.0 } F{fast}
    {% else %}
        G0 Z{ [cur_z+1.0, max_z]|min } F{fast}
    {% endif %}
    
    ##############  Move to the dock  ##############    
    ROUNDED_G0 X={x} Y={tool.params_safe_y} D=0 F={fast}         # Move to the right safe Y position
    {% if 'z' in path[0] %}                                       # For changers with stationary docks
        ROUNDED_G0 Z={z + path[0]['z']|float} D=20 F={fast}       ## Move to the first point in the path, in the z axis
    {% endif %}                                                   # Regardess,
    ROUNDED_G0 Y={y + path[0]['y']|float} D=0 F={fast}            # Move to the first point in the path, in the y axis
    STOP_TOOL_PROBE_CRASH_DETECTION
    
    ############## Run the path ##############
    {% for pos in path %}
        G0 X{x + pos['x']|float} Y{y + pos['y']|float} F{tool.params_path_speed|float * (pos.get('f', 1.0)|float) }
    {% endfor %}
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

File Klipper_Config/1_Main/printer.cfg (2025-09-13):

[include mainsail.cfg]
## default macros
[include misschanger_macros/config_switch.cfg]
[include misschanger_macros/homing.cfg]
[include misschanger_macros/nozzle_clean.cfg]
[include misschanger_macros/overwrite.cfg]
[include misschanger_macros/print_time_default.cfg]
[include misschanger_macros/tool_calibrate.cfg]
[include misschanger_macros/toolchanger.cfg]
[include misschanger_macros/offsets_adjust_record.cfg]
# ## optional default macros
# [include misschanger_macros/tool_calibrate_extra.cfg]    # For the Nudge probe
## misschanger settings
[include misschanger_settings.cfg]
## Other macros
[include macro-general.cfg]
[include macro-testing.cfg]
# ...
# ...
# ...

####################################################################################
##	                         Others
####################################################################################
[config_switch]
[pause_resume]
[save_babies]
# ...
# ...
# ...

####################################################################################
##	                         Global Variables
####################################################################################
#--------------------------------------------------------------------
[gcode_macro _static_variable]
description: Global static variables that is used through out the configs
## Tool-head calibration
variable_calibration_probe_x: 241.237500     # X aproximate position of the calibration probe. CHANGE TO MATCH YOUR SET-UP
variable_calibration_probe_y: 329.825000     # Y aproximate position of the calibration probe. CHANGE TO MATCH YOUR SET-UP
variable_calibration_safe_z: 50.00           # Z aproximate safe position of the calibration probe. KEEP CONSERVATIVE TO AVOID COLLISION
variable_calibration_min_z: 30.00            # Z aproximate probe position of the calibration probe.
variable_probe_stable_time: 1000             # Time (in ms) to wait for calibration probe to reset. Default: 1000
variable_calibration_abs_z_seperately: 0     # "0" = False / "1" = True. For, the Nudge probe this should be '1'
variable_final_lift_z: 3                     # This must be the same as "final_lift_z" in [tools_calibrate] in misschanger_settings.cfg
## Cleaning dock
variable_clean_dock_x: 0                     # Set to "0" to disable. X aproximate position of the cleaning dock. CHANGE TO MATCH YOUR SET-UP.
variable_clean_speed: 7000                   # Don't set too high, the violent shaking may cause problems. CHANGE TO MATCH YOUR SET-UP.
variable_clean_temp: 200                     # Nozzle clean temperature.
variable_clean_threshold: 150.0              # The minimum perimeter of the print, below which no mid-print cleaning of the nozzle will occur.
## Always on crash detection
variable_alway_on_crash_detection: 0         # "0" = False (off) / "1" = True (on)
## For heatsoak macro
variable_heatsoak_temp: 0                    # Set to "0" to disable. Chamber temperature target for heat soak. REQUIRES [temperature_sensor Chamber] below.
## Dynamic thermal expansion compensation
variable_thermo_expand_offset: -0.080        # Maximum z offset for thermal expansion compensation. REQUIRES [temperature_sensor Chamber]
variable_thermo_expand_temp_high: 70         # Chamber temp to apply maximum z offset for thermal expansion compensation. REQUIRES [temperature_sensor Chamber]
variable_thermo_expand_temp_low: 0           # Set to "0" to disable. Chamber temp start applying thermal expansion compensation. REQUIRES [temperature_sensor Chamber]
## Fan control
variable_nm_ciculation_speed: 1.00           # Nevermore Stealth Max fan speed in circulation mode
variable_nm_exhaust_speed: 1.00              # Nevermore Stealth Max fan speed in exhaust mode
variable_chamber_ciculation_speed: 0.25      # Chamber fan speed in chamber-heating mode
variable_chamber_temp_threshold: 91          # If bed temp is below this temperature, then don't enable chamber-heating mode
gcode:                                       # This is here to appease klipper
# ...
# ...
# ...

####################################################################################
##	                 Temperature Monitoring
####################################################################################
[temperature_sensor Chamber]
sensor_type: Generic 3950
sensor_pin: PF4
# ...
# ...
# ...

####################################################################################
##                  FAN
####################################################################################
#--------------------------------------------------------------------
[fan_generic fan_nevermore_stealthmax]
pin: PD13
max_power: 1.0
shutdown_speed: 0.0
cycle_time: 0.010
hardware_pwm: False
kick_start_time: 0.100
off_below: 0.05

#--------------------------------------------------------------------
[fan_generic fan_chamber_heater]
pin: PA8
max_power: 1.0
shutdown_speed: 0.0
cycle_time: 0.010
hardware_pwm: False
kick_start_time: 0.100
off_below: 0.05
# ...
# ...
# ...

####################################################################################
##                          Session Variables
####################################################################################
#;<    # Section Variable marker
#---------------------------------------------------------------
[include ./T0-SB2209-Revo-LDO.cfg]
[include ./T1-SB2209-Revo-LDO.cfg]
[include ./T2-Nitehawk-Revo-G2E.cfg]
[include ./T3-Nitehawk-Revo-LDO.cfg]
#---------------------------------------------------------------
[gcode_macro _home]
variable_xh: 175.0
variable_yh: 235.0
# Dock is installed: True or False
variable_dock: True
gcode:
#---------------------------------------------------------------
[bed_mesh]
speed: 200                   # Calibration speed
horizontal_move_z: 10        # Z-axis movement speed
mesh_min: 30,130             # Minimum calibration point coordinates x, y
mesh_max: 320, 320           # Maximum calibration point coordinates x, y. 350mm=320,320
probe_count: 11,11           # Number of sampling points (7X7 is 49 points)
mesh_pps: 2,2                # Number of supplementary sampling points
algorithm: bicubic           # algorithmic model
bicubic_tension: 0.2         # Algorithmic interpolation don't move
#---------------------------------------------------------------
[quad_gantry_level]
# Gantry Corners for 350mm Build
gantry_corners:
	-60,-10
	410,420
# Probe points
points:
	50,130
	50,300
	300,300
	300,130

speed: 150                   # Levelling speed
horizontal_move_z: 15        # Z-axis starting height
retries: 10                  # Number of out-of-tolerance retries
retry_tolerance: 0.0075      # Sampling tolerance
max_adjust: 20               # Maximum adjustment stroke for levelling

#*# <---------------------- SAVE_CONFIG ---------------------->
#*# DO NOT EDIT THIS BLOCK OR BELOW. The contents are auto-generated.
#*#
#*# [tool_probe T0]
#*# z_offset = -0.563750
#*#
#*# [extruder]
#*# control = pid
#*# pid_kp = 35.987
#*# pid_ki = 4.284
#*# pid_kd = 75.574
#*#
#*# [tool T1]
#*# gcode_x_offset = 0.000
#*# gcode_y_offset = 0.000
#*# gcode_z_offset = 0.000
#*#
#*# [tool_probe T1]
#*# z_offset = 0.000
#*#
#*# [extruder1]
#*# control = pid
#*# pid_kp = 33.912
#*# pid_ki = 3.325
#*# pid_kd = 86.477
#*#
#*# [tool T2]
#*# gcode_x_offset = 0.000
#*# gcode_y_offset = 0.000
#*# gcode_z_offset = 0.000
#*#
#*# [tool_probe T2]
#*# z_offset = 0.000
#*#
#*# [extruder2]
#*# control = pid
#*# pid_kp = 27.329
#*# pid_ki = 1.804
#*# pid_kd = 103.505
#*#
#*# [tool T3]
#*# gcode_x_offset = 0.000
#*# gcode_y_offset = 0.000
#*# gcode_z_offset = 0.000
#*#
#*# [tool_probe T3]
#*# z_offset = 0.000
#*#
#*# [extruder3]
#*# control = pid
#*# pid_kp = 34.630
#*# pid_ki = 3.785
#*# pid_kd = 79.217
#*#

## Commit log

2024-02-18 First release
    [BOM.ods]
2024-04-09 New Ideas
    [BOM.ods]
2024-05-17 Test update
    [T0-SB2209-Revo-LDO.cfg, T1-SB2209-Revo-LDO.cfg, homing-TC.cfg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]
2024-05-26 New Design
    The old design has been abandoned due to the inherent flaws in it. The new design is inspired by the StealthChanger.
    [homing.cfg, macro-print.cfg, macro-tc-SAVE_CONFIG.cfg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]
2024-05-26 New design
    [homing.cfg, macro-print.cfg, macro-tc-SAVE_CONFIG.cfg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]
2024-05-30 Add toolchange config
    [T0-SB2209-Revo-LDO.cfg, T1-SB2209-Revo-LDO.cfg, homing.cfg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]
2024-06-11 reorganise and add instructions
    [Settings_1_printer-single.cfg, Settings_2_printer-multi.cfg, T0-SB2209-Revo-LDO.cfg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]
2024-06-21 Add Nudge and probe test
    [Probe accuracy.ods, calibrate-offsets.cfg]
2024-06-27 Add missing stl and update sample configs
    [Settings_1_printer-single.cfg, Settings_2_printer-multi.cfg, T0-SB2209-Revo-LDO.cfg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]
2024-06-30 Update config files and documentation
    [config_no_dock.cfg, config_no_dock_backup.cfg, config_wt_dock.cfg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]
2024-07-02 Update Software configs and add instructions
    [T0-SB2209-Revo-LDO.cfg, T1-SB2209-Revo-LDO.cfg, calibrate-offsets.cfg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]
2024-07-03 update instructions
    [calibrate-offsets.cfg]
2024-07-07 Update sample config and add instructions
    [T0-SB2209-Revo-LDO.cfg, T1-SB2209-Revo-LDO.cfg, calibrate-offsets.cfg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]
2024-07-12 Update config and add more instructions
    [T0-SB2209-Revo-LDO.cfg, T1-SB2209-Revo-LDO.cfg, macro-print.cfg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]
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2024-07-13 Bug fix
    Fix the bug that cause rehoming failures when a toolhead that is not the reference is mounted.
    [homing.cfg]
2024-07-16 Update intructions
    [toolchanger.cfg]
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2024-07-30 Beta
    - Finished the instruction
    - Fix bugs in the sample config
    - Add latest input shaper test results
    - Add official support for the Phaetus Dragon hotend
    [T0-SB2209-Revo-LDO.cfg, T2-RP2040-Dragon-Step.cfg, calibrate-offsets.cfg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]
2024-08-09 Add v1.1 CADs and update documentations
    This release initiate the next version of MissChanger v1.1.
    It also adds the a roadmap to the frontpage.
    [Filament Compatibilty Results.ods]
2024-09-12 Add notes for filament tests and more
    [T0-SB2209-Revo-LDO.cfg, T1-SB2209-Revo-LDO.cfg, T2-RP2040-Dragon-Step.cfg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]
2024-09-28 update v1.1 documentation
    [T0-SB2209-Revo-LDO.cfg, T1-SB2209-Revo-LDO.cfg, T2-RP2040-Dragon-Step.cfg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]
2024-09-28 Update material test writing
    [Filament Compatibilty Results.ods]
2024-09-28 Update test report
    [Filament Compatibilty Results.ods]
2024-10-19 Repo reorganised and add support for NM StealthMax
    Reduce the number of step files in the repo, to stay under GitHub storage limit.
    Adding the documentation supporting the optional Nevermore StealthMax
    [Probe accuracy.ods]
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2024-11-30 Updates
    More hardware
    1. Add G2E support.
    Software changes:
    2. `CALIBRATE_OFFSETS` will now only calibrate gcode offsets.
    3. `CALIBRATE_NPO` can now be directed to a specific tool-head. Leaving it blank will resulted in all tool-heads being calibrated.
    4. Update how crash detection is handled. Preventing Klipper crashes whene there is a failed pick up.
2024-12-02 Update CADs and fix bug
    1. Update Dock Mount CAD
    2. Fix the bug where the hotend heater is turn off when docked.
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2025-01-01 Add usermod and update documentations
    [Lubeballs_Probe-Bottom_Wire_Channel V2_.step]
2025-02-04 Update documentation and Implement design feedback
    [Lubeballs_Probe-Bottom_Wire_Channel_V2 (implemented).step]
2025-02-09 Bug fixes and add Stealthchanger mod
    [SC_TH-side_mod.step, SC_TH-side_mod.stl, Shuttle MGN12 (With belt grooves).stl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]
2025-02-09 Usermod for Stealthchanger
    [SC_TH-side_mod.step, SC_TH-side_mod.stl, Shuttle MGN12 (With belt grooves).stl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]
2025-02-09 Miss Stealthchanger
    [SC_TH-side_mod.step, SC_TH-side_mod.stl, Shuttle MGN12 (Without belt grooves).stl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]
2025-03-19 Getting ready for beta part 2
    [Probe accuracy.ods]
2025-03-22 Reorganise
    Reduce the size of the project, by moving legacy files to a public network folder.
    [10_NM_StealthMax_Mod-FlowChamber_Mod.step, 10_NM_StealthMax_Mod-Intake_Funnel_x4.step, 10_NM_StealthMax_Mod-Output_Funnel.step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]
2025-03-24 Idle dock mount by Psychosis5150
    [Dock Mount.stl, Lubeballs_Probe-Bottom_Wire_Channel_V2 (implemented).step, MissChanger Dock Mount v3.step]
2025-03-29 clean-up and organise
    [10_NM_StealthMax_Mod-FlowChamber_Mod.step, 10_NM_StealthMax_Mod-Intake_Funnel_x4.step, 10_NM_StealthMax_Mod-Output_Funnel.step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]
2025-04-01 Move the test result to the wiki
    [Probe accuracy.ods]
2025-04-04 Repo management
    [1.3a_BowdenCap_Closed_x2.stl, 1.4a_CableEntryCap_M8Barrel.stl, 10_NM_StealthMax_Mod_v3-Intake_Funnel_x4.stl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]
2025-04-16 Add chamber fan control feature
    [printer.cfg]
2025-04-28 update backend
    The new Python backend requires the fan object to be format differently
    [T0-SB2209-Revo-LDO.cfg, T1-SB2209-Revo-LDO.cfg, T2-Nitehawk-Revo-G2E.cfg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]
2025-05-04 Ready for hot-fix
    [1.3a_BowdenCap_Closed_x2.stl, 1.4a_CableEntryCap_M8Barrel.stl, 10_NM_StealthMax_Mod_v3-FlowChamber_Mod.stl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]
2025-05-04 Ready for hot fix 2
    [1.3a_BowdenCap_Closed_x2.stl, 1.4a_CableEntryCap_M8Barrel.stl, 10_NM_StealthMax_Mod_v3-FlowChamber_Mod.stl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]
2025-05-04 Ready for hot fix 3
    [T0-SB2209-Revo-LDO.cfg, T1-SB2209-Revo-LDO.cfg, T2-Nitehawk-Revo-G2E.cfg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]
2025-05-04 Hot fix beta and add feature
    Major software hot fix, see: https://github.com/VIN-y/klipper-toolchanger/pull/32#issue-3038225470
    [T0-SB2209-Revo-LDO.cfg, T1-SB2209-Revo-LDO.cfg, T2-Nitehawk-Revo-G2E.cfg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]
2025-06-08 Update descriptions
    [printer.cfg]
2025-07-09 Reduce difficulty of making the endstops assem.
    [Endstops_Assembly-v0.6.step, Endstops_Assembly-v0.6.stl, Endstops_Mount.stl]
2025-07-11 Simplify directory structure
    [1.3a_BowdenCap_Closed_x2.stl, 1.4a_CableEntryCap_M8Barrel.stl, 10_NM_StealthMax_Mod_v3-FlowChamber_Mod.stl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]
2025-07-11 Release v1.2.2
    [T0-SB2209-Revo-LDO.cfg, T1-SB2209-Revo-LDO.cfg, T2-Nitehawk-Revo-G2E.cfg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]
2025-07-23 Update MissChanger_Assembly_Manual.pdf
    Add additional description of the wiring of the Lube Balls.
2025-09-06 Updated Bar Ends Holder
    Better performing / easier to build:
    - Use M3 nuts instead of threaded inserts.
    - Increase clamp gap.
    - Optimise built-in supports.
    [Bar Ends Holder A v1_9.step, Bar Ends Holder B v1_9.step, Bar_Ends Holder_A v1_9.stl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]
2025-09-06 Update T&C TH-side
    - Update instruction
    - use M3 nuts instead of threaded inserts.
    - include a Mono option, for ease of manufacturing.
    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
    [Tap&Change-Front_TH_Side.stl, Tap&Change-Front_TH_Side_Mono.3mf, Tap&Change-v3.1_TH_Side.step]
2025-09-06 Update sample config
    [macro-general.cfg, macro-testing.cfg]
2025-09-12 Update printer.cfg
    Typo correction: changed 'marcos' to 'macros' in two places
    [printer.cfg]
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
